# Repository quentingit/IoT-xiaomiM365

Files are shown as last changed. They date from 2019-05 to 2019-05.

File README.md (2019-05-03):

# Xiaomi M365 SecureBOX
<p align="center">
  
</p>

## Introduction
Turn signal and blind spot detection for Xiaomi M365

## Hardware requirements
- Wemos D1 Mini (ESP8266, Arduino-compatible layout, wifi, 80/160Mhz, 4Mb flash)<BR>
<p align="center">
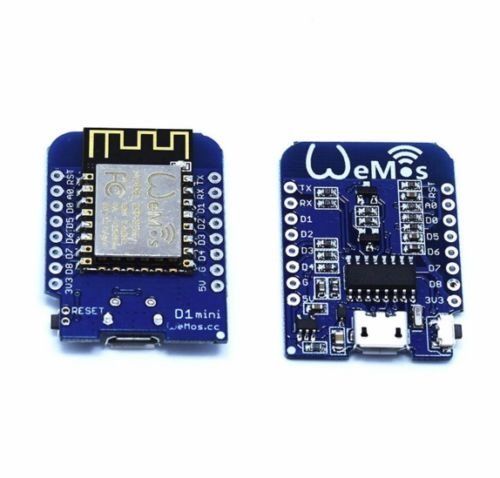
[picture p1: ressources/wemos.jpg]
  
</p>

- Led strip composed of 14 leds (5V)

- Sonar HC-SR04 or DYP-ME007V1 (5V)
<p align="center">
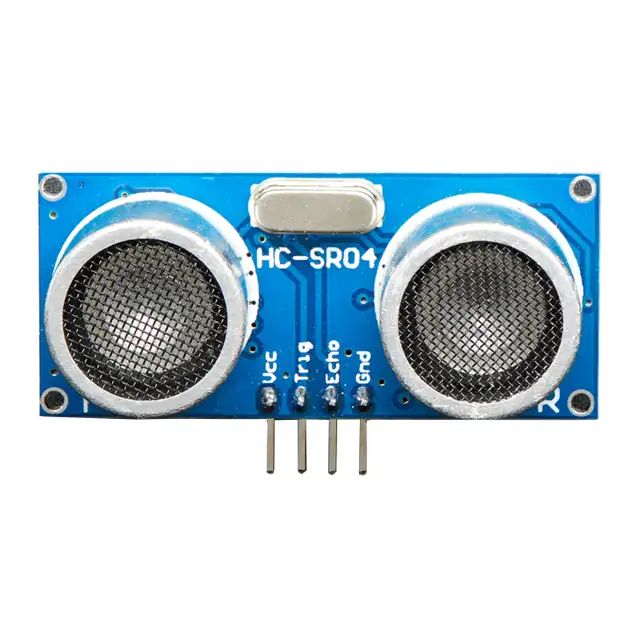
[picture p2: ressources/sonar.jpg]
  
</p>

- The  Android application, used to control remotly the electric scooter
<p align="center">
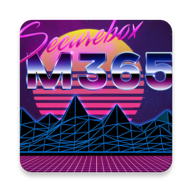
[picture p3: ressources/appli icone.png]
  
</p>
The application connect to the Xiaomi M365 with the bluetooth protocol.<br>
This allow the Wemos (the web server) to retreive the speed of the electric scooter.<br>
Here is a screenshot with the interface with the blinking controls, the electric scooter battery and the speed in real time :<br>
<br>
<p align="center">
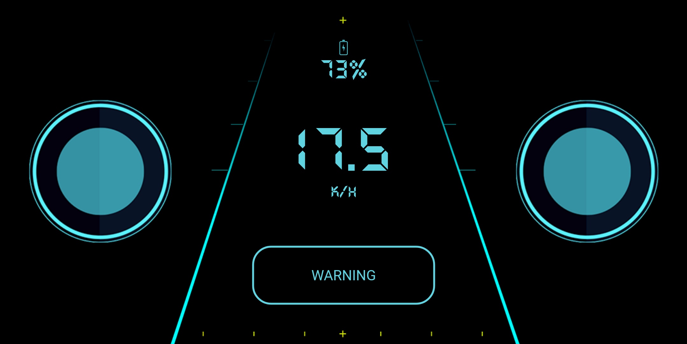
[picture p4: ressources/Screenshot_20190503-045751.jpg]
  
</p>

## Software requirements

[Arduino IDE with ESP8266 platform installed](https://www.arduino.cc/en/main/software)

If you use windows / OSx you will probably need drivers: [Wemos Driver](https://www.wemos.cc/downloads)

### Library 
- Adafruit_NeoPixel (for the leds)
- ESP8266WiFi (for the Wifi)
- QuickMedianLib (for the median filter)

### External library
- ESP8266FS (SPIFFS, see: [Using ESP8266 SPIFFS tutorial](https://www.instructables.com/id/Using-ESP8266-SPIFFS/) )

### Android app library
Links usefuls for the androidapp:<br>
- Communicate with xiaomi for get parameters  : https://github.com/maisi/M365-Power
- webview bridge library to communicate between android (java) and webview (js): https://github.com/lzyzsd/JsBridge

## How does it work ?
<p align="center">
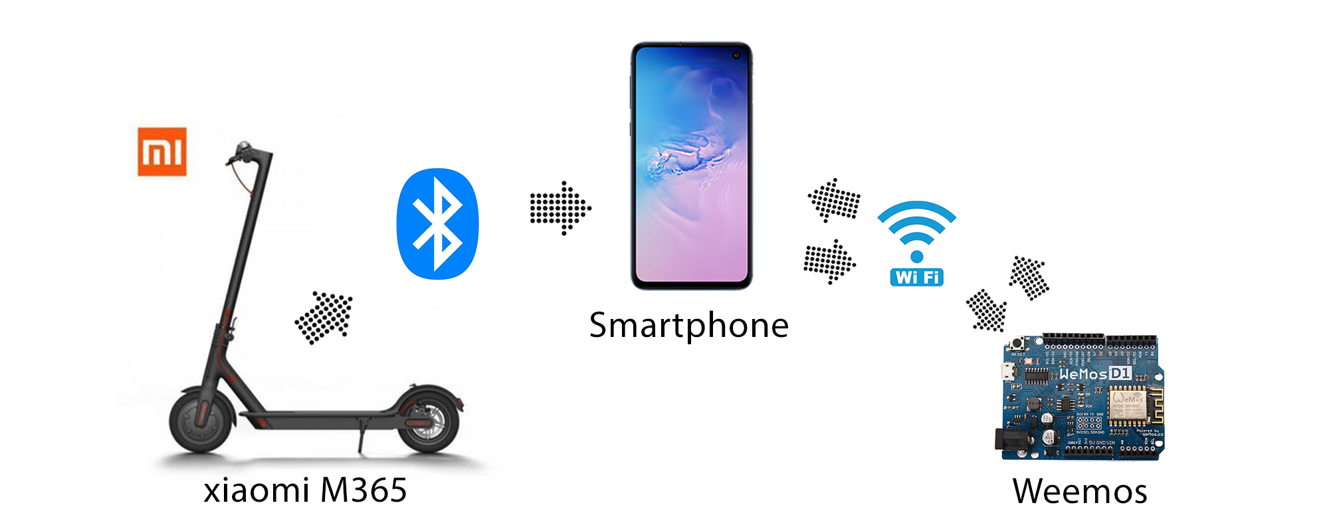
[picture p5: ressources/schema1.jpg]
  
</p>
The electric scooter Xiaomi M365 have a bluetooth connection that can be used to get some informations like the actual speed, the battery. This is sent to the android application.<br>
The Wemos is connected to the phone wifi hotspot, and so the can connect it via the android application from a webview. The android application is a bridge from the bluetooth to the web interface.
<br>
<p align="center">
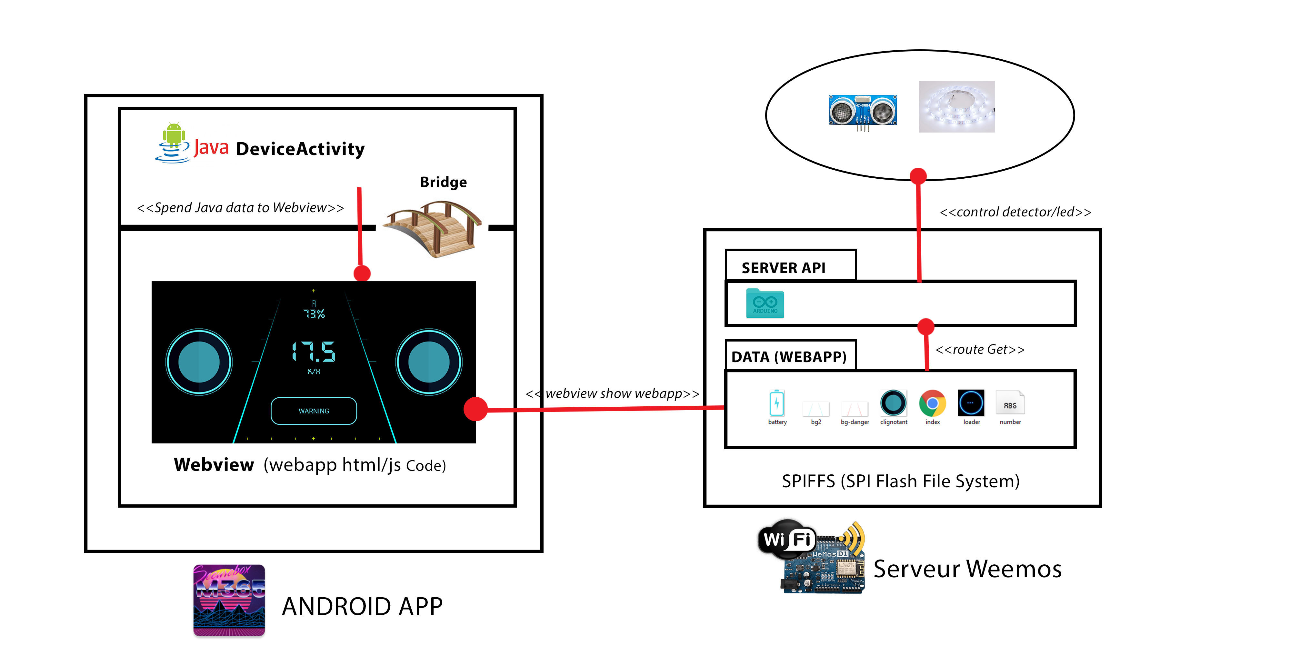
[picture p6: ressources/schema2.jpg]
  
</p>

### Wiring
Firstly, the Arduino card connect on a WiFi network. Modify the SSID and Password at the top of the code.<br>
Secondly, use the diagram bellow the connect the sonar (enabling blind spot detection) and the led strip (enabling turn signal and warning signal) <br>

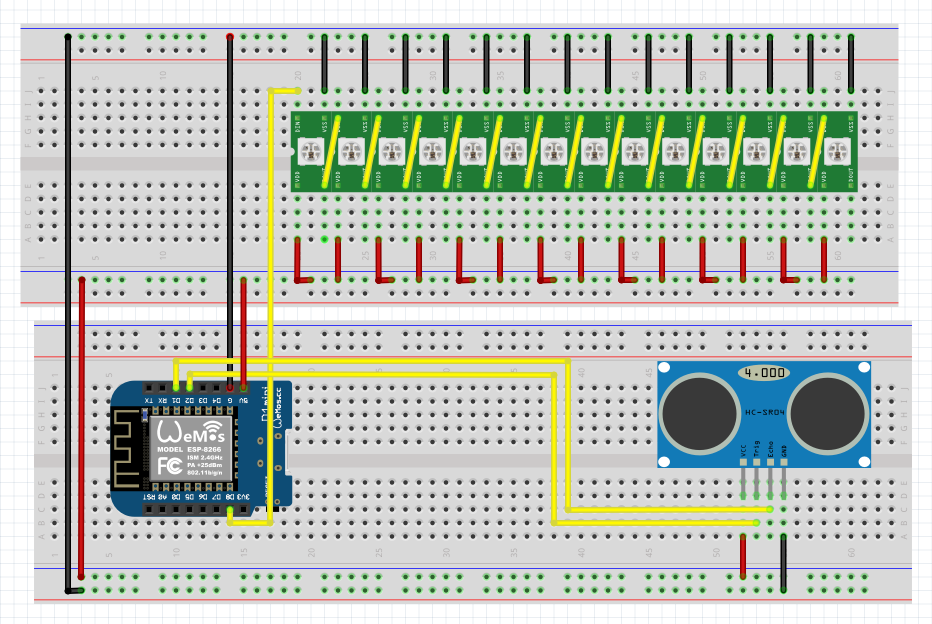
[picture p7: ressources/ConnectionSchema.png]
Conneciton schema

You can found the original file in `ressources/Connection.fzz`

## Issues

### The sonar HC-SR04 / DYP-ME007V1 filtering
<br>
While using the sonar HC-SR04 or DYP-ME007V1 we had problems with the echo signal. The original signal had random peaks (green signal on the picture bellow), like noise. We do not want this peaks as it is generating a bad blind spot detection randomly, even when we put a condition at 120CM or less to engage the blind spot signal.<br>
<br>
To solve this problem, we put 2 additionnal signals :<br>
-The median of the 15 last values of the original signal (blue)<br>
-The moving average of the 15 last values of the original signal (red)<br>
<br>

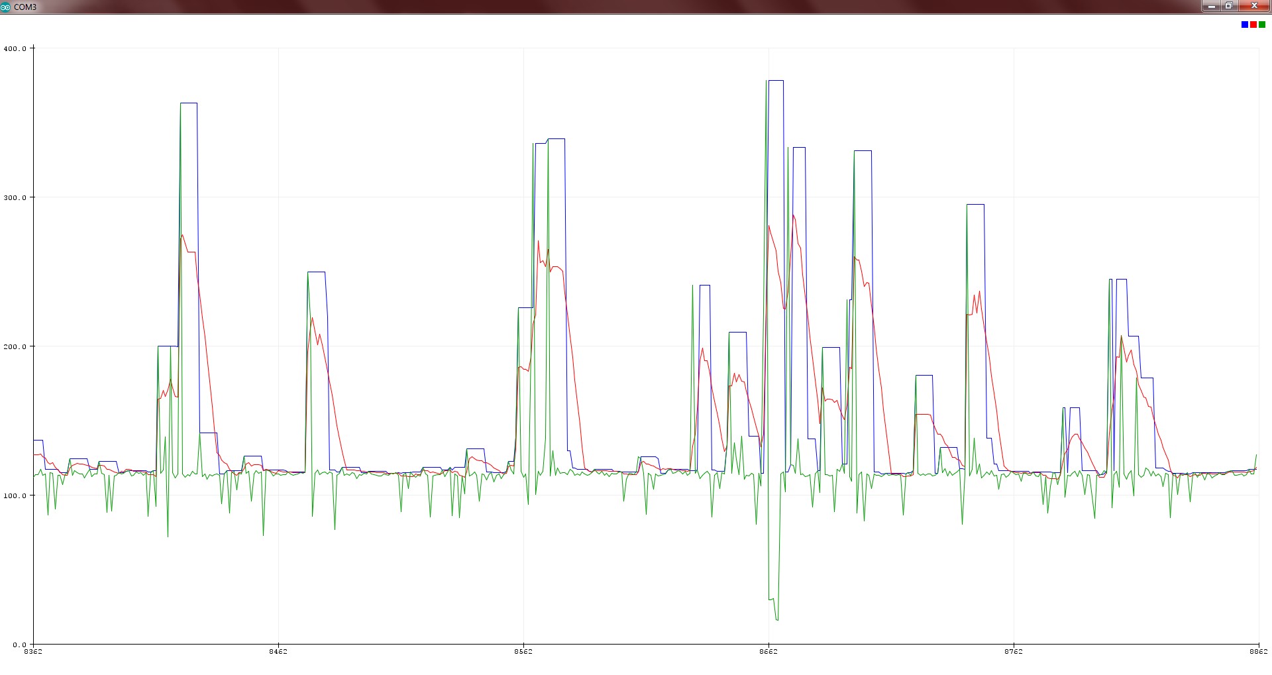
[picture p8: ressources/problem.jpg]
Problem sonar


<br>
As we can see on the picture above, an array of 15 values is not enought for making the signal flat and removing the noise we do not want. Let's try with 30 values :<br>
<br>

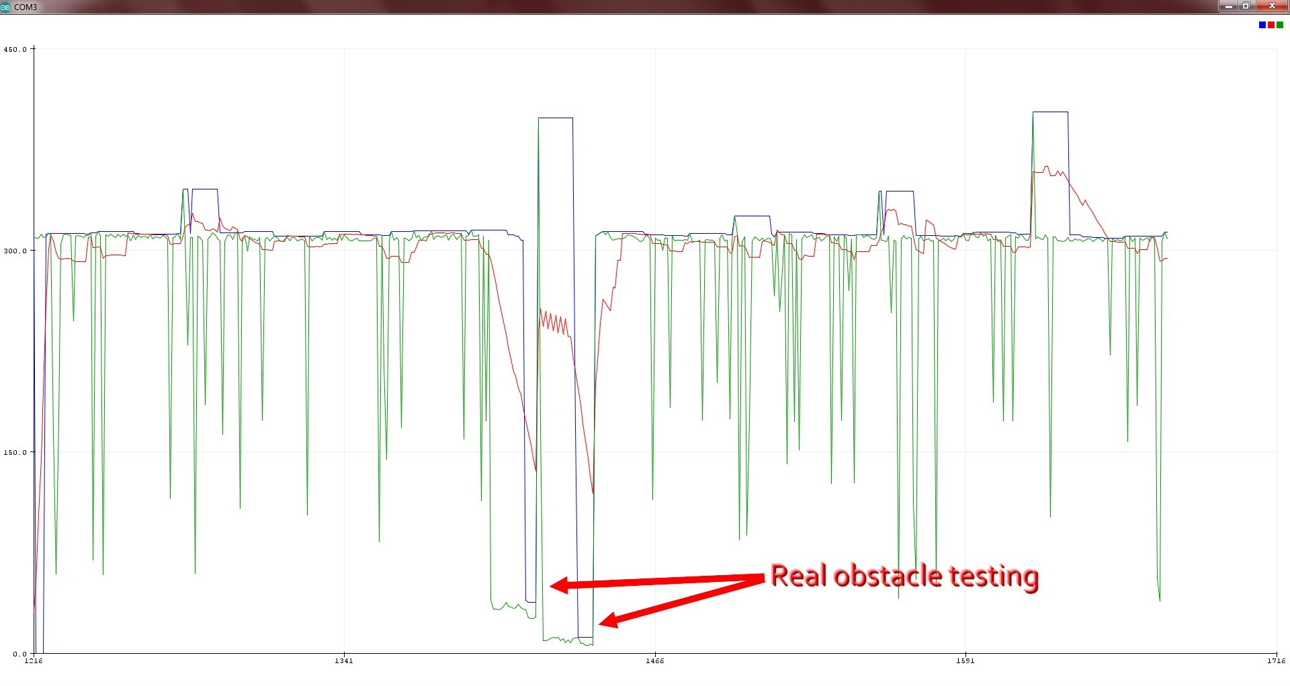
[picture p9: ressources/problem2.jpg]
Problem sonar 2


<br>
While trying to simulate an obstacle, we saw that it was slow to detect the signal, almost 2/3 of the real signal (green) is lost because of the median filter if we use it.<br>
We have been searching the perfect value and we have found that 20 is a good value :<br>
<br>

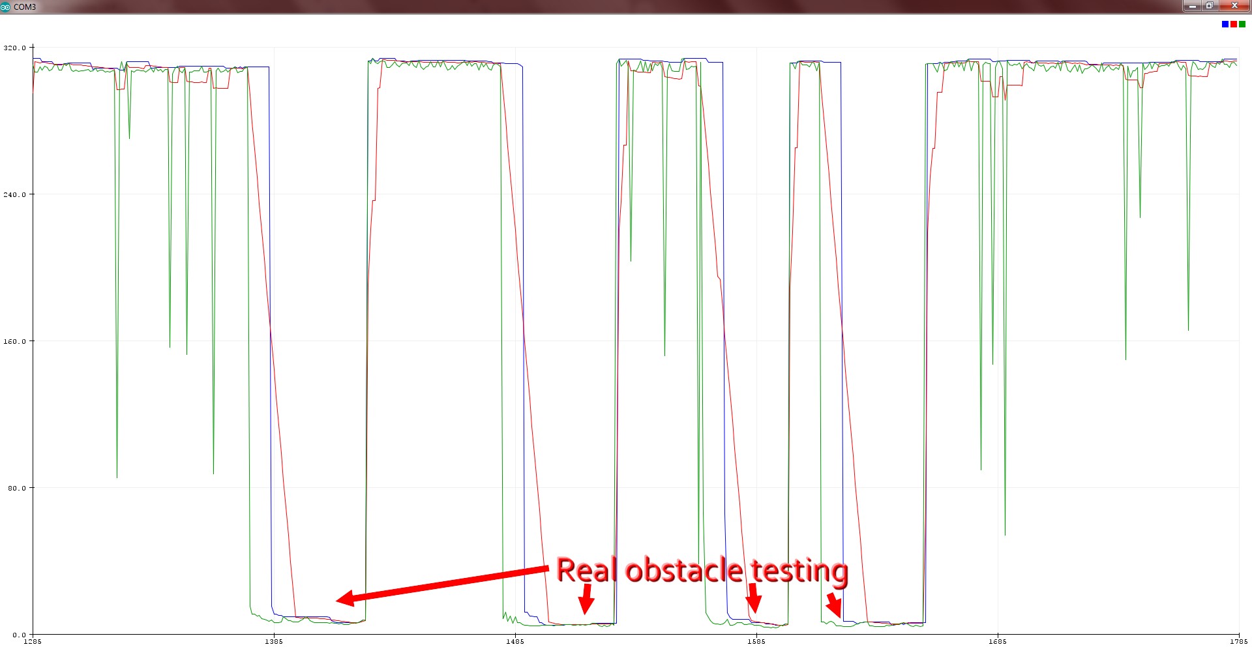
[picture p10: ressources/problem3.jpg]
Problem sonar 3


<br>
Both the moving average and the median are removing most of the peaks that we do not want here. As the median is more "flat", we used this signal to solve the problem.<br>

# Building the SecureBox

<p align="center">
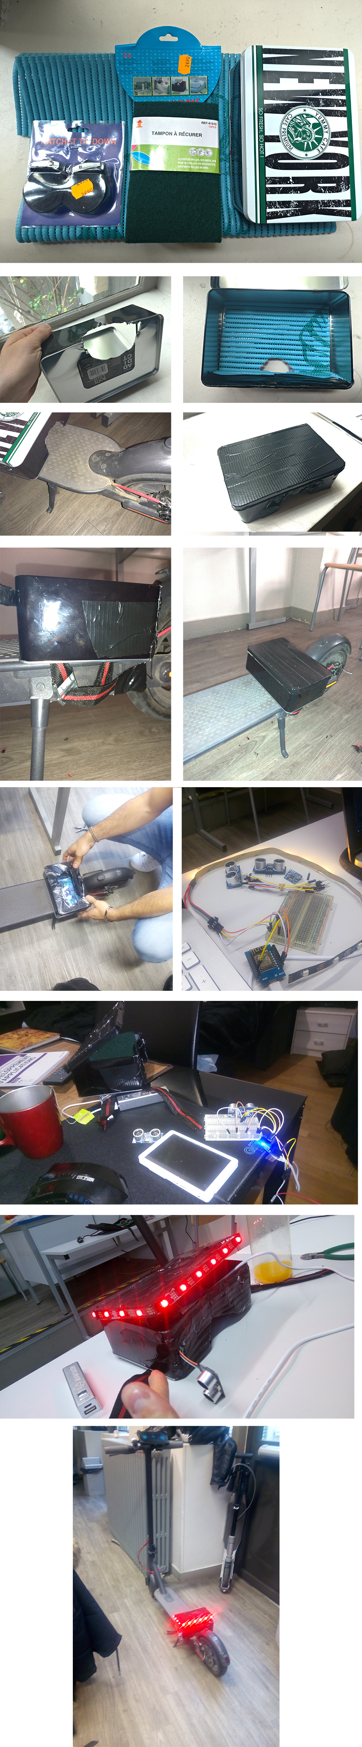
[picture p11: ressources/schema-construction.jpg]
  
</p>

## Video of the prototype

[Click here to see the video](https://drive.google.com/file/d/1nNjBMYanGiluA92XC430YwJ56WK5rWbO/view?usp=sharing)

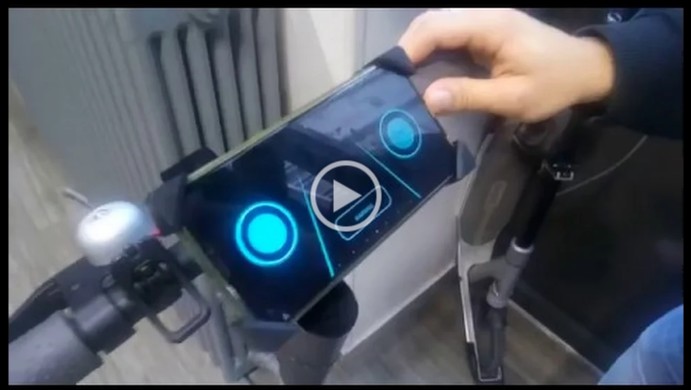
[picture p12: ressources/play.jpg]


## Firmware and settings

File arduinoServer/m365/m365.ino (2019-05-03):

// ===================================== LEDS
#include <Adafruit_NeoPixel.h>
// ===================================== BLIND SPOT SENSOR
#include "QuickMedianLib.h"
float valuesHistory[20];
float valuesHistoryLen = sizeof(valuesHistory) / sizeof(float); // see doc for QuickMedianLib
int HistorySize = 20;
// ===================================== WIFI + SERVER + FS
#include <ESP8266WiFi.h>
#include <WiFiClient.h>
#include <ESP8266WebServer.h>
#include <ESP8266mDNS.h>
#include <FS.h>

#define DBG_OUTPUT_PORT Serial

#ifndef STASSID
#define STASSID "a"
#define STAPSK  "lalalalala"
#endif

const char* ssid = STASSID;
const char* password = STAPSK;
const char* host = "esp8266fs";

ESP8266WebServer server(80);
//holds the current upload
File fsUploadFile;

// ===================================== LEDS
#define PIN D8
#define SIZE 14
Adafruit_NeoPixel strip = Adafruit_NeoPixel(14, PIN, NEO_GRB + NEO_KHZ800); // 14 LEDS in the strip
bool blink = false;

// Fill the dots one after the other with a color
void colorWipe(uint32_t c, uint16_t start, uint16_t end) {
  for (uint16_t i = start; i < end; i++) {
    strip.setPixelColor(i, c);
  }

  strip.show();
}

void turnOff() {
  colorWipe(strip.Color(0, 0, 0), 0, 14);
}

void turnRight() {
  colorWipe(strip.Color(255, 70, 0), 0, 7); // 7 leds orange at right ->
}

void turnLeft() {
  colorWipe(strip.Color(255, 70, 0), 7, 14); // 7 leds orange at left <-
}

void warnings() {
  colorWipe(strip.Color(255, 70, 0), 0, 14); // 14 orange warning leds <->
}

void Break() {
  colorWipe(strip.Color(255, 0, 0), 0, 14); // 14 red warning leds <->
}

int delaycount = 0;
int action = 0;
// ===================================== BLIND SPOT SENSOR
const unsigned long MEASURE_TIMEOUT = 25000UL; // TIMEOUT : 12ms = ~4m (340m/s)
const float SOUND_SPEED = 340.0 / 1000; // sound speed in the air in mm/µs
int delaylight = 0;
// =====================================
//format bytes
String formatBytes(size_t bytes) {
  if (bytes < 1024) {
    return String(bytes) + "B";
  } else if (bytes < (1024 * 1024)) {
    return String(bytes / 1024.0) + "KB";
  } else if (bytes < (1024 * 1024 * 1024)) {
    return String(bytes / 1024.0 / 1024.0) + "MB";
  } else {
    return String(bytes / 1024.0 / 1024.0 / 1024.0) + "GB";
  }
}

String getContentType(String filename) {
  if (server.hasArg("download")) {
    return "application/octet-stream";
  } else if (filename.endsWith(".htm")) {
    return "text/html";
  } else if (filename.endsWith(".html")) {
    return "text/html";
  } else if (filename.endsWith(".css")) {
    return "text/css";
  } else if (filename.endsWith(".js")) {
    return "application/javascript";
  } else if (filename.endsWith(".png")) {
    return "image/png";
  } else if (filename.endsWith(".gif")) {
    return "image/gif";
  } else if (filename.endsWith(".jpg")) {
    return "image/jpeg";
  } else if (filename.endsWith(".ico")) {
    return "image/x-icon";
  } else if (filename.endsWith(".xml")) {
    return "text/xml";
  } else if (filename.endsWith(".pdf")) {
    return "application/x-pdf";
  } else if (filename.endsWith(".zip")) {
    return "application/x-zip";
  } else if (filename.endsWith(".gz")) {
    return "application/x-gzip";
  }
  return "text/plain";
}

bool handleFileRead(String path) {
  DBG_OUTPUT_PORT.println("handleFileRead: " + path);
  if (path.endsWith("/")) {
    path += "index.html";
  }
  String contentType = getContentType(path);
  String pathWithGz = path + ".gz";
  if (SPIFFS.exists(pathWithGz) || SPIFFS.exists(path)) {
    if (SPIFFS.exists(pathWithGz)) {
      path += ".gz";
    }
    File file = SPIFFS.open(path, "r");
    server.streamFile(file, contentType);
    file.close();
    return true;
  }
  return false;
}




/*
void handleFileUpload() {
  if (server.uri() != "/edit") {
    return;
  }
  HTTPUpload& upload = server.upload();
  if (upload.status == UPLOAD_FILE_START) {
    String filename = upload.filename;
    if (!filename.startsWith("/")) {
      filename = "/" + filename;
    }
    DBG_OUTPUT_PORT.print("handleFileUpload Name: "); DBG_OUTPUT_PORT.println(filename);
    fsUploadFile = SPIFFS.open(filename, "w");
    filename = String();
  } else if (upload.status == UPLOAD_FILE_WRITE) {
    //DBG_OUTPUT_PORT.print("handleFileUpload Data: "); DBG_OUTPUT_PORT.println(upload.currentSize);
    if (fsUploadFile) {
      fsUploadFile.write(upload.buf, upload.currentSize);
    }
  } else if (upload.status == UPLOAD_FILE_END) {
    if (fsUploadFile) {
      fsUploadFile.close();
    }
    DBG_OUTPUT_PORT.print("handleFileUpload Size: "); DBG_OUTPUT_PORT.println(upload.totalSize);
  }
}

void handleFileDelete() {
  if (server.args() == 0) {
    return server.send(500, "text/plain", "BAD ARGS");
  }
  String path = server.arg(0);
  DBG_OUTPUT_PORT.println("handleFileDelete: " + path);
  if (path == "/") {
    return server.send(500, "text/plain", "BAD PATH");
  }
  if (!SPIFFS.exists(path)) {
    return server.send(404, "text/plain", "FileNotFound");
  }
  SPIFFS.remove(path);
  server.send(200, "text/plain", "");
  path = String();
}

void handleFileCreate() {
  if (server.args() == 0) {
    return server.send(500, "text/plain", "BAD ARGS");
  }
  String path = server.arg(0);
  DBG_OUTPUT_PORT.println("handleFileCreate: " + path);
  if (path == "/") {
    return server.send(500, "text/plain", "BAD PATH");
  }
  if (SPIFFS.exists(path)) {
    return server.send(500, "text/plain", "FILE EXISTS");
  }
  File file = SPIFFS.open(path, "w");
  if (file) {
    file.close();
  } else {
    return server.send(500, "text/plain", "CREATE FAILED");
  }
  server.send(200, "text/plain", "");
  path = String();
}

*/


///////////////////////////////////////////////////////
//GLOBAL STATE FOR DETECTOR CARS
String stateDetector;

//GLOBAL SPEED TROTINETTE , INITIALIZE TO 0 
String speed="11";



void handleWarning() {

  String warning;
    if ( server.hasArg("warning") ) {
        warning = server.arg(0);

        DBG_OUTPUT_PORT.printf("warning :%s" , warning.c_str());
        //INSTRUCTIONS : WARNING A METTRE ICI

        if(warning=="0"){
        //on fais clignotter
          Serial.println("WARNING ON <->");
          action = 3;
        }
        if(warning=="1"){
         //on arrete
         Serial.println("WARNING STOP");
         action = 0;
        }
        
      
    } else {
        Serial.println("Bad URL.");
        server.send(404, "text/plain", "Bad URL.");
        return;
    }

}




void handleLeftBlinking() {
 String leftBlinking;
    if ( server.hasArg("leftblinking") ) {
        leftBlinking = server.arg(0);
        DBG_OUTPUT_PORT.printf("<- leftBlinking : %s" , leftBlinking.c_str());


        //INSTRUCTIONS : WARNING A METTRE ICI

        if(leftBlinking=="0"){
        //on fais clignotter
          Serial.println("LIGHT <-");
          action = 1;
        }
        if(leftBlinking=="1"){
         //on arrete
         Serial.println("LIGHT STOP");
         action = 0;
        }
        
      
    } else {
        Serial.println("Bad URL.");
        server.send(404, "text/plain", "Bad URL.");
        return;
    }

}



void handleRightBlinking() {
    String rightBlinking;
    if ( server.hasArg("rightblinking") ) {
        rightBlinking = server.arg(0);
        DBG_OUTPUT_PORT.printf("rightBlinking : %s" ,rightBlinking.c_str());

        //INSTRUCTIONS : WARNING A METTRE ICI

        if(rightBlinking=="0"){
        //on fais clignotter
          action = 2;
          Serial.print("LIGHT ->");
        }
        if(rightBlinking=="1"){
         //on arrete
         Serial.println("LIGHT STOP");
         action = 0;
        }
        
      
    } else {
        Serial.println("Bad URL.");
        server.send(404, "text/plain", "Bad URL.");
        return;
    }
}




void handleSpeed() {

    if ( server.hasArg("speed") ) {

        //UPDATE SPEED      
        speed = server.arg(0);
        DBG_OUTPUT_PORT.printf("speed : %s" , speed.c_str());
     
    } else {
        Serial.println("Bad URL.");
        server.send(404, "text/plain", "Bad URL.");
        return;
    }

}


//RETURN STATE DETECTOR RESPONSE
void handleDistance() {
   Serial.println("State Dector response");
   server.send(200, "text/plain", stateDetector);
   return;
  
}

////////////////////////////////////////////////////////


/*
void handleFileList() {
  if (!server.hasArg("dir")) {
    server.send(500, "text/plain", "BAD ARGS");
    return;
  }


  String path = server.arg("dir");
  DBG_OUTPUT_PORT.println("handleFileList: " + path);
  Dir dir = SPIFFS.openDir(path);
  path = String();

  String output = "[";
  while (dir.next()) {
    File entry = dir.openFile("r");
    if (output != "[") {
      output += ',';
    }
    bool isDir = false;
    output += "{\"type\":\"";
    output += (isDir) ? "dir" : "file";
    output += "\",\"name\":\"";
    output += String(entry.name()).substring(1);
    output += "\"}";
    entry.close();
  }

  output += "]";
  server.send(200, "text/json", output);
}
*/
void setup(void) {
  DBG_OUTPUT_PORT.begin(115200);
  DBG_OUTPUT_PORT.print("\n");
  DBG_OUTPUT_PORT.setDebugOutput(true);
  SPIFFS.begin();
  {
    Dir dir = SPIFFS.openDir("/");
    while (dir.next()) {
      String fileName = dir.fileName();
      size_t fileSize = dir.fileSize();
      DBG_OUTPUT_PORT.printf("FS File: %s, size: %s\n", fileName.c_str(), formatBytes(fileSize).c_str());
    }
    DBG_OUTPUT_PORT.printf("\n");
  }


  //WIFI INIT
  DBG_OUTPUT_PORT.printf("Connecting to %s\n", ssid);
  if (String(WiFi.SSID()) != String(ssid)) {
    WiFi.mode(WIFI_STA);
    WiFi.begin(ssid, password);
  }

  while (WiFi.status() != WL_CONNECTED) {
    delay(500);
    DBG_OUTPUT_PORT.print(".");
  }
  DBG_OUTPUT_PORT.println("");
  DBG_OUTPUT_PORT.print("Connected! IP address: ");
  DBG_OUTPUT_PORT.println(WiFi.localIP());

  MDNS.begin(host);
  DBG_OUTPUT_PORT.print("Open http://");
  DBG_OUTPUT_PORT.print(host);
  DBG_OUTPUT_PORT.println(".local/edit to see the file browser");



/////////////////////////////////////////////////////////////////////////////////////////
  //SERVER INIT

  //activate/ desactivate warning
  server.on("/warning", HTTP_GET, handleWarning);


  //activate/ desactivate rightblinking
  server.on("/rightblinking", HTTP_GET, handleRightBlinking);


  //activate/ desactivate leftblinking
  server.on("/leftblinking", HTTP_GET, handleLeftBlinking);


  //update speed for cars distance 
  server.on("/carsdistance", HTTP_GET, handleSpeed);


  //verify cars distance (thanks to the previous route to have speed)
  //we activate car detector only if speed is > 10  
  server.on("/carsdistance", HTTP_GET, handleDistance);


////////////////////////////////////////////////////////////////////////////////////////////
   
  //list directory
  //server.on("/list", HTTP_GET, handleFileList);
  //load editor
  //server.on("/edit", HTTP_GET, []() {
  //  if (!handleFileRead("/edit.htm")) {
  //    server.send(404, "text/plain", "FileNotFound");
  //  }
  //});
  //create file
  //server.on("/edit", HTTP_PUT, handleFileCreate);
  //delete file
  //server.on("/edit", HTTP_DELETE, handleFileDelete);
  //first callback is called after the request has ended with all parsed arguments
  //second callback handles file uploads at that location
  //server.on("/edit", HTTP_POST, []() {
  //  server.send(200, "text/plain", "");
  //}, handleFileUpload);

  //called when the url is not defined here
  //use it to load content from SPIFFS
  server.onNotFound([]() {
    if (!handleFileRead(server.uri())) {
      server.send(404, "text/plain", "FileNotFound");
    }
  });

  //get heap status, analog input value and all GPIO statuses in one json call
  /*server.on("/all", HTTP_GET, []() {
    String json = "{";
    json += "\"heap\":" + String(ESP.getFreeHeap());
    json += ", \"analog\":" + String(analogRead(A0));
    json += ", \"gpio\":" + String((uint32_t)(((GPI | GPO) & 0xFFFF) | ((GP16I & 0x01) << 16)));
    json += "}";
    server.send(200, "text/json", json);
    json = String();
  });*/

  // ===================================== TURNING INDICATORS INIT
  strip.begin();
  strip.show(); // Initialize all leds to 'off'
  // ===================================== BLIND SPOT INIT
  pinMode(D2, OUTPUT); // TRIGGER_PIN
  digitalWrite(D2, LOW); // TRIGGER_PIN should be LOW when not using
  pinMode(D1, INPUT); // ECHO_PIN
  // =====================================
  
  server.begin();
  DBG_OUTPUT_PORT.println("HTTP server started");

}






//////////////////////////////////////////////////////////////////////


     

void loop(void) {

  // Check the speed of the vehicle
  if( speed.toInt() > 10 ){
    // ===================================== BLIND SPOT DETECTION
    /* start to measure with HIGH PULSE of 10µs in TRIGGER PIN */
    digitalWrite(D2, HIGH); // trigger pin
    delayMicroseconds(10);
    digitalWrite(D2, LOW); // trigger pin
  
    /* measure time between pulse and ECHO */
    long measure = pulseIn(D1, HIGH, MEASURE_TIMEOUT); // ECHO_PIN
  
    /* calculation of the distance... */
    float distance_cm = (measure / 2.0 * SOUND_SPEED) / 10.0;
  
    //Serial.println("0 400 "); // MAX
    Serial.println(distance_cm);
    if (distance_cm)
    {
      // shifting history of CM values
      for(int i = 0;i<HistorySize;i++)
      {
        if(!valuesHistory[(HistorySize-2)-i]) valuesHistory[(HistorySize-1)-i] = distance_cm;
        valuesHistory[(HistorySize-1)-i] = valuesHistory[(HistorySize-2)-i];
      }
      valuesHistory[0] = distance_cm;
      float med = QuickMedian<float>::GetMedian(valuesHistory, valuesHistoryLen);
      //Serial.print(med); // CM DISTANCE MEDIAN
      //Serial.print(" ");
      float moy = 0;
      for(int i=0;i<HistorySize;i++){ moy += valuesHistory[i]; }
      moy = moy / HistorySize;
      //Serial.print(moy); // CM DISTANCE AVERAGE
      //Serial.print(" ");
      //Serial.println(distance_cm, 2); // CM DISTANCE
      if ( med < 120 )
      {
        Serial.print("CAR DETECTED!! (");
        Serial.print(med);
        Serial.println(")");
        stateDetector = "1"; // DETECTED
      } 
      else 
      {
        Serial.print("NOTHING!! ("); // TEMP
        Serial.print(med);
        Serial.println(")");
        stateDetector = "0"; // NOTHING
      }
    } else stateDetector = "0"; // NOTHING
  } else stateDetector = "0"; // NOTHING
                  
  server.handleClient();
  MDNS.update();

  // ===================================== TURN LIGHT INDICATION
  if (delaycount == 10) delaycount = 0;
  if (delaycount == 0)
  { 
    if (blink == true)
    { 
      Serial.print("BLINKING. action=");
      Serial.println(action);
      if ( action == 1 ) turnLeft();
      if ( action == 2 ) turnRight();
      if ( action == 3 ) warnings();
      if ( stateDetector == "1" ) Break();
      blink = false;
    }
    else
    {
      turnOff();
      /*if ( distance_cm >= 120 ) {
        turnOff();
      }*/
      blink = true;
    }
  }

  // ===================================== COUNTERS
  delaycount++;
  delaylight++;

  delay(40);
}

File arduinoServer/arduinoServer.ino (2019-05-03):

// ===================================== LEDS
#include <Adafruit_NeoPixel.h>
// ===================================== BLIND SPOT SENSOR
#include "QuickMedianLib.h"
float valuesHistory[20];
float valuesHistoryLen = sizeof(valuesHistory) / sizeof(float); // see doc for QuickMedianLib
int HistorySize = 20;
// ===================================== WIFI
#include <ESP8266WiFi.h>
// ===================================== LEDS
#define PIN D8
#define SIZE 14
Adafruit_NeoPixel strip = Adafruit_NeoPixel(14, PIN, NEO_GRB + NEO_KHZ800); // 14 LEDS in the strip
bool blink = false;

// Fill the dots one after the other with a color
void colorWipe(uint32_t c, uint16_t start, uint16_t end) {
  for (uint16_t i = start; i < end; i++) {
    strip.setPixelColor(i, c);
  }

  strip.show();
}

void turnOff() {
  colorWipe(strip.Color(0, 0, 0), 0, 14);
}

void turnRight() {
  colorWipe(strip.Color(255, 70, 0), 0, 7); // 7 leds orange at right ->
}

void turnLeft() {
  colorWipe(strip.Color(255, 70, 0), 7, 14); // 7 leds orange at left <-
}

void Break() {
  colorWipe(strip.Color(255, 0, 0), 0, 14); // 14 red warning leds
}

int delaycount = 0;
int action = 0;
// ===================================== BLIND SPOT SENSOR
const unsigned long MEASURE_TIMEOUT = 25000UL; // TIMEOUT : 12ms = ~4m (340m/s)
const float SOUND_SPEED = 340.0 / 1000; // sound speed in the air in mm/µs
int delaylight = 0;
// ===================================== WIFI
const char* ssid = "ESGI"; // your network name (SSID)
const char* password = "Reseau-GES"; // your network password

WiFiServer server(80);
// Variable to store the HTTP request
String header;
// Auxiliar variables to store the current output state
String output5State = "off";
String output4State = "off";

// Assign output variables to GPIO pins
const int output5 = 5;
const int output4 = 4;
// ===================================== WEB SERVER
const uint16_t HTTPPort = 80;
const byte maxURL = 50;
char urlRequest[maxURL + 1]; // +1 for '\0'
long timeThresold = 0;
WiFiClientSecure clientSecure;
WiFiServer serveurWeb(HTTPPort); // create http server on standard port

void printHTTPServerInfo()
{
  Serial.println("==============================");
  Serial.print(F("SERVER URL: http://"));
  Serial.print(WiFi.localIP());
  if (HTTPPort != 80) {
    Serial.print(F(":"));
    Serial.print(HTTPPort);
  }
  Serial.println();
  Serial.println("==============================");
}

void requestListener()
{
  WiFiClient client = server.available();   // Listen for incoming clients

  if (client) {                             // If a new client connects,
    Serial.println("New Client.");          // print a message out in the serial port
    String currentLine = "";                // make a String to hold incoming data from the client
    while (client.connected()) {            // loop while the client's connected
      if (client.available()) {             // if there's bytes to read from the client,
        char c = client.read();             // read a byte, then
        Serial.write(c);                    // print it out the serial monitor
        header += c;
        if (c == '\n') {                    // if the byte is a newline character
          // if the current line is blank, you got two newline characters in a row.
          // that's the end of the client HTTP request, so send a response:
          if (currentLine.length() == 0) {
            // HTTP headers always start with a response code (e.g. HTTP/1.1 200 OK)
            // and a content-type so the client knows what's coming, then a blank line:
            client.println("HTTP/1.1 200 OK");
            client.println("Content-type:text/html");
            client.println("Connection: close");
            client.println();

            // turns the GPIOs on and off
            if (header.indexOf("GET /5/on") >= 0) {
              Serial.println("GPIO 5 on");
              output5State = "on";
              digitalWrite(output5, HIGH);
            } else if (header.indexOf("GET /5/off") >= 0) {
              Serial.println("GPIO 5 off");
              output5State = "off";
              digitalWrite(output5, LOW);
            } else if (header.indexOf("GET /4/on") >= 0) {
              Serial.println("GPIO 4 on");
              output4State = "on";
              digitalWrite(output4, HIGH);
            } else if (header.indexOf("GET /4/off") >= 0) {
              Serial.println("GPIO 4 off");
              output4State = "off";
              digitalWrite(output4, LOW);
            }

            // Display the HTML web page
            client.println("<!DOCTYPE html><html>");
            client.println("<head><meta name=\"viewport\" content=\"width=device-width, initial-scale=1\">");
            client.println("<link rel=\"icon\" href=\"data:,\">");
            // CSS to style the on/off buttons
            // Feel free to change the background-color and font-size attributes to fit your preferences
            client.println("<style>html { font-family: Helvetica; display: inline-block; margin: 0px auto; text-align: center;}");
            client.println(".button { background-color: #195B6A; border: none; color: white; padding: 16px 40px;");
            client.println("text-decoration: none; font-size: 30px; margin: 2px; cursor: pointer;}");
            client.println(".button2 {background-color: #77878A;}</style></head>");

            // Web Page Heading
            client.println("<body><h1>ESP8266 Web Server</h1>");

            // Display current state, and ON/OFF buttons for GPIO 5
            client.println("<p>GPIO 5 - State " + output5State + "</p>");
            // If the output5State is off, it displays the ON button
            if (output5State == "off") {
              client.println("<p><a href=\"/5/on\"><button class=\"button\">ON</button></a></p>");
            } else {
              client.println("<p><a href=\"/5/off\"><button class=\"button button2\">OFF</button></a></p>");
            }

            // Display current state, and ON/OFF buttons for GPIO 4
            client.println("<p>GPIO 4 - State " + output4State + "</p>");
            // If the output4State is off, it displays the ON button
            if (output4State == "off") {
              client.println("<p><a href=\"/4/on\"><button class=\"button\">ON</button></a></p>");
            } else {
              client.println("<p><a href=\"/4/off\"><button class=\"button button2\">OFF</button></a></p>");
            }
            client.println("</body></html>");
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

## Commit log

2019-05-03 Mise à jour de la documentation
2019-05-03 Functions for turning right and turning left
    All leds are OK
2019-05-03 Commentaire dans le code, ajout schéma électrique
    [Connection.fzz]
2019-05-03 Added support SONAR + 1,20M detection RED LIGHTS
2019-05-03 SENSOR UPDATE
    [Connection.fzz]
2019-05-03 Median filter on SONAR 100% Working
2019-05-03 adding sonar picture to doc
2019-05-03 updating image size sonar
